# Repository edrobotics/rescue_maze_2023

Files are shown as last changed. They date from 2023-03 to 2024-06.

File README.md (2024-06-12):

# Rescue Maze 2023

Repository for ED Robotics' participation in Robocup Junior Rescue Maze 2023.

The code was used in the RoboCup SM (Swedish championships) and in the RoboCup worldchampionship in Bordeaux. 

## Scores: 

- RoboCup Junior Sweden 2023: first place

- RoboCup Junior 2023: top 10 (or tenth place if you prefer it that way) 

- RoboCup Junior 2023 superteam: third place together with Bot Ugl-EE from Australia

## Notes:

It was our first year doing Robotics, so please enjoy the spaghetti<!---and don't forget the sauce-->.

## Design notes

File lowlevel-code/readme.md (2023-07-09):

# Auriga (lowlevel) code
This code is for the code running on the auriga, which includes sensor interaction, motion system, and rescue kit mechanism.
The competition is now over, so hopefully nothing in here will have to be touched ever again.

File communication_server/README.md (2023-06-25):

# README
This application is the server handling communication between the programs on the raspberry pi as well as the communication between the raspberry pi and the auriga.

In its current state, it is just some code put together as a base and it does not work yet.

In "communication_protocol.md", the communication standards are written down.

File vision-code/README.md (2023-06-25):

#Vision code folder
This code will run on the Raspberry Pi

to start
python3 control_class.py

to move programs to pi if git is not working
./rsyncmaze.sh
#you have to edit local path

to move log from pi 
./updatelog.sh
#edit local path aswell

to move last run to a folder
python3 archiv_log.py

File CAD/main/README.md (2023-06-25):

# Main CAD files
This is the folder for all CAD files except for the rescue kit mechanism.

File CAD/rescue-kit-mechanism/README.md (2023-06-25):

#Resue Kit Mechanism CAD files
This is the folder for the CAD files for the rescue kit mechanism.

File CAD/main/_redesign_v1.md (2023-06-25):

# Redesign v1
This is the first redesign after the swedish competition

# Problems with old design
- Robot jumping/skipping when turning
- Turning was not really around center point.
- High CG - the robot is constantly close to tipping over when driving on ramps
- Difficult to work on the robot
    - Wires inaccessible -> cannot secure them, among other things
    - Time-consuming to disassemble
    - Annoying to change battery
- Lack of space for rescue kit mechanism
- Rescue kit mechanism prone to breaking
- Battery cable touching wheel while driving
- Electrical connections not always shielded
- Not enough space for raspberry pi camera ribbon cable

Unsure/speculation/potential problems
- Front sensor may be positioned too low and may be too narrow and too unstable
- Too small FOV for the camera

# General improvements
Certain:
- Lower CG
    - Power the raspberry off of the main battery
    - Put the pi lower down
    - Try to sink everything down a bit into the baseplate.
    - Place dummy weights down low?
    - Longer wheelbase - would make turning worse
    - Alternative solution to lower CG: Add some kind of support wheels which engage only when the robot is tipping too much. A challenge to keep them away from the walls during normal operation.
        - Wild idea: Use servos or similar to control the arms
    - Alternative solution to lower CG: Drive slower up the ramp (if even possible?)
    - Move voltage converters lower down.
- Make the robot easier to work on
    - Improve ease of (dis)assembly - not everything should be connected by the same screws. Not too many components per screw.
    - Make the top come off -> can access everything easier
        - Slice the pillars somewhere above the ultrasonics
        - Mount the mirror to the top, with arms comming down
- Mount the encoder motor drivers better. Remove pins and make housing.
- Add possibility to stabilize the rescue kit tower by connecting it to the pillars
- Add lighting to the camera

Maybe:

# New notes

Hold the mirror with two arms going down on each side, fastening where the support legs meet the rest of the body.

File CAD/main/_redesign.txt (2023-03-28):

Things to change/update/add in the redesign:

/Move the back motors inwards and increase the spacing to an appropriate amount
/Move the ultrasonic sensors inwards a bit
	/The front bracket can be partly under the auriga
/Maybe put ultrasonic sensors sideways to improve camera view?

/Make the baseplate thicker
	/-> Enables the battery to be sunken in if needed
	-> Allows space for the rescue kit mechanism

/Battery mounting:
	/Remove the baseplate and make the battery mount separate
	
Colour sensor mounting:
	Flap that can move up and down
	
/Rescue-kit mechanism mounting:
	XSome removable plate in the back
	/Mounting holes for plate added.
	
Mirrors go on top of the auriga. The same assembly could hold the mirrors

/The carrying handle can Go on the back, alternatively from front and back up to middle

Fixes:
/The slot for the ledring could be a bit larger and the supports in front could clamp down from above
/The holes for the pi should be deeper

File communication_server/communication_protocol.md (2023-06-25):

# Communication protocol - sockets
Communication is always initialized by the client sending a request.
After the client has sent a request, serialServer will either fetch the requested data or execute the given command.

In general, every request should be answered with the requested data (if there is any) and then some message signalling that the command was executed.

Maybe every request should be terminated by some special character (like \n)?

## Requests

### Drive step
Drives one step in the maze.
- Arduino function - driveStep()
- Arguments - none
- Return - whether or not a full step was driven. Returned as '1' or '0' (as strings/chars), as well as the ground colour of the tile that would have been driven on. Also the reason for not driving a full step?
  - Reasons can be odometry error, ground colour, error detecting the wall with the ultrasonic etc.
  - TODO: What should the maze program do if there has been an error in the odometry? Does it need any other data from the auriga?
- Request - "!driveStep"

### Turn steps
Turns the specified amount of steps (not yet implemented) in the specified direction.
- Arduino function - turnSteps()
- Arguments - the direction to turn (cw or ccw)
- Return - none
- Request - "!turnSteps, *direction*"
    - *direction* - cw (clockwise) or ccw (counterclockwise)

### Get wall states
Returns the current state of the walls around the robot
- Arduino function - getWallStates()
- Arguments - none
- Return - String containing comma-separated 0 and 1 representing if the walls are present (1 is present) in the format: "*front*, *left*, *right*", where front, left and right are the values for the corresponding walls
- Request - "!getWallStates"

### Rescue kits (to be done)

### Get victim state
Returns whether or not a victim has been detected (and how long ago the response was?)
- Arguments - none (maybe maximum time since last discovery?)
- Return - The victim type and whether it is on the right or left side of the robot.
  - "*victimType*, *victimSide*"
- Request - "!getVictimState"

Note: The code will probably check if it has a victimState stored and how long ago it was stored. Then there will be another process/thread (?) which responds to the vision program and updates these variables which can then be used in other ways.

One problem with storing the victimstate is that if the robot turns, the directions will no longer be correct. Maybe this program should also keep track of absolute direction (given by the maze-code in every command altering direction?). Maybe it will not be a problem if we never use victim data that is too old.

General about vision - The program on the auriga will need to be able to stop in the middle of a driveStep to detect a victim, and the maze-code (and this server) will need to be able to accomodate that as well.

### Update victim state
Gives data to serialServer about victim type and position. Sent from the vision-code.
- Arguments - "*victimType*, *victimSide*"
- Return - None
- Request - "!updateVictimState, *victimType*, *victimSide*"

# Communication protocol - serial
This section handles the communication between serialServer and the auriga.

## General communication format
Data will either be sent as chars and the termination character will be '\n'.

Commands: !\<command>,\<data>'\n'

Return: !a,\<data>

Return !s (success) or !f (failed) when done with an action

!b may be used for sending debugging information from the auriga to the raspberry (?).

## Commands
- !d - driveStep
  - Return:
- !t,\<direction> - turn
  - direction - which way to turn. 'r' (right), 'l' (left)
- !k,\<amount> - drop rescue kit
  - amount - the amount of rescue kits to deploy (maybe not used?)
- !w - getWallStates
  - !a,\<walldata> - walldata is a byte where the 3 last bits represent the wall states. 0b\<front>\<left>\<right>. 1 is present, 0 is not present.
- !i - interrupt the current action
- !r - resume the current action after an interrupt

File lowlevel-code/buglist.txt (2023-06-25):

When driving away from a wall, sometimes the back wall change is not detected and the front one is used instead

When doing gyroturnsteps, it sometimes turns the wrong amount. WHY?

The first gyroturn without a preceeding drivestep could have some zero-variables

When driving onto a colour, the robot stops too late

Communication features to implement:
Tell colours (sort of done)
Tell if ramp driven up

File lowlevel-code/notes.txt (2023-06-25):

Make a function to calculate the difference between any angles - can replace some code present now.

gyroTurn() - can turn more than 180 degrees. Divide it into < 180 degree segments.

General - add some way of filtering out unreasonable results and falling back to "dumb" methods in those cases.

General - if I call the MeUltrasonicSensor::distanceCm() too rapidly, will the distances update every time?

The method to check for wall changes will have to be updated - right now it will fail if a sensor mistakenly measures so wrong that the wallPresence changes.
    Maybe calculate some kind of average and round it to 1 or 0? (so that a temporary error won't destroy everything)

Design of driveStep(): Should the checks modify trueDistanceDriven or should they just break and then the program will decide outside of the loop whether the distance has been drive or not?

Note: I modified the source code of MeUltrasonicSensor.cpp to be able to specify the maximum distance measurement

Note: The last thing that worked alright (?) was not checking the back sensors for wallchanges. The problem with interference did appear (even though it should have).

Check colour sensor (and others) in getUltrasonics.

Instead of moving every measurement in the array, keep the current index and just change that value. Could also calculate the average more efficiently.

Calculation of the current angle for use in the next angle should be separated out into its own function.

How and when is g_gyroOffset updated?

Add a requirement that trueDistanceDriven is close enough to what it will be corrected to when a wallchange is detected

When driving backwards, the detected wallchanges will be wrong. To do correctly, make an expression taking the target distance into account (or the starting distance, or maybe just special case for driving backwards)

Bugs:

Sometimes when the robot is close to a wall, it drives slowly forward and sometimes does not recognise the wall. (potentially fixed?)

Sometimes when the robot is driving without walls and you correct it (maybe something else is triggering it), it drives in a circle and does not drive backwards when it is stopped.
The trueDistanceDriven seems to be wrong (oscillates because the robot is driving in a circle)
Why is the robot not correcting accordingly with the data? The angles must be wrong (is this the same issue as the bug below?)

When the robot is going backwards, something seems to go wrong with the angles (it makes a "three point turn" but with an arbitrary amount of points and the oscillation gets larger every time)

Sometimes the robot does not correct the right amount when turning.

Sometimes (often?) when a backwallchange should be detected it is not and the frontwallchange is used instead.

The robot does not seem to stop directly when detecting a new ground colour - instead it looks like it always drives the 30cm it should. Why is that?
Should have been fixed. Was probably caused by an inverted return statement (but I have NOT tested if it works now!)

Other (not necessarily bugs, but things to fix):
In driveStep(), when the first measurements are taken, the robot only uses one wall even if both are present.

After you have stopped, flush the distance arrays and update the robotAngle somehow. This should also be done before and after turning.

The driveStepDriveLoop takes too much time. How can I improve it?
    Make the getUltrasonics() function take less time
    Perhaps not calculate the angle every time (how much time does it take?)- just the difference? Then calculate the angle only when needed (say when you left the wall you calculate the angle based on the previous data. also in the end)

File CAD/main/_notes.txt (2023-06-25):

TODO:
Check ultrasonic sensor heights
Addd a front ramp to aid in driving over speedbumps
Idea - add small wheell beside the coloursensor -> it can sit down low and still be safe from impact, because the wheels will lift it if it drives over something

General:

Holesize is maybe a bit to small
	On the creator 3 it is OK, a bit tight, on the Prusa Mini it is too tight (you can still screw it through though)

Ultrasonic sensors:

The ultrasonic sensors should be higher up or could be angled slightly upwards to avoid falsely detecting a ramp as a wall.

Baseplate:

Ska båda motorkonfigurationer fungera med samma basplatta?

Om plasten ej fungerar kan CNC-maskinen vara ett alternativ

Ska måttet som anges vara för hjulbasens mått eller för basplattans?

For threaded inserts: https://hackaday.com/2019/02/28/threading-3d-printed-parts-how-to-use-heat-set-inserts/

Gör mount-stället för ultrasonic sensor brackets smalare (på hödjden)?

Improvements for next print:
	Add holes for rescue kit mechanism

Batteri + hållare:

För att byta batteriet: Borde kunna dra mellan hjulen

För att hålla fast batteriet: Kanter i sidan. Någon form av rem ovanför för tryck nedåt. Alternativt tryckplatta?

Rescue kit mechanism:

Perhaps use rack and pinion for the pusher for the rescue kit mechanism?

Use some heavier weight and put on top to make the rescue kits go down more reliably?

Design ideas:
	Have a rescue kit holder (like a well) with an extended "backwards" edge. A rescue kit is in the well, it moves, the rescue kit drops out as another one drops onto the "backwards" edge. When the mechanism retracts, the rescue kit on the "backwards" edge is pushed into the well by the back wall. This works both with linear and rotational motion.

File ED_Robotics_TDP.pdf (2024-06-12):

## ROBOCUPJUNIOR RESCUE (MAZE) 2023

## TEAM DESCRIPTION PAPER

## ED Robotics

### Abstract

This paper describes our robot, as well as the development process of it. The robot is a junior rescue maze robot capable of completing most tasks that are within the rules. It is a fourwheeled encoder-motor driven robot controlled by a Raspberry Pi and a Makeblock Me Auriga (Arduino Mega). Positioning is done using two ultrasonic sensors on each side and one in front, and the rescue kit mechanism is in the back. For detecting victims, the robot uses a camera looking down on two mirrors, which split the image into two, enabling us to see both walls simultaneously. The strong sides of the robot, besides being cute, are advanced pose estimation, aligning itself well to the maze, optimization of memory usage and a reliable rescue kit mechanism.

### 1. Introduction

### a. Team

The name of our team is ED Robotics, and our members and their roles are as follows:

QUAK123 – Responsible for rescue kit mechanism. Prior experiences include programming games, mobile and web applications. Worked on CAD projects in school.

apollen85 – Responsible for the motion system. This includes the hardware design (excluding the rescue kit mechanism), electronics and local maze navigation (for example turning exactly 90O). Experience was gained through experimenting with simple Arduino projects and doing CAD projects at home and in school, but organized and complicated projects like this one have not been attempted before. Programming was selftaught.

c4tm4n/"bohrmeister” – Responsible for the vision system and the raspberry Pi. This includes detecting coloured and visual victims and handling the raspberry Pi. Past experiences include python programming and Linux skills.

MrK – Responsible for maze navigation and mapping. This is also the master code which communicates with the other programs, and it also navigates the robot through the maze, maps the maze, and gets the robot back to the start tile. Had previous experience in programming, both from selflearning, for instance from making games, and from school.

### 2. Project Planning a. Overall Project Plan

As this is our first extensive and collaborative project, our overall aim for the competition is learning about collaboration and robotics as well as building a well-performing robot.

During the early stages of development, not much of a plan existed. However, we realised that we needed to spend much time as early as possible. Later on, our work became more organized. A schedule was made and evaluations were made throughout. Different roles were assigned and defined, which enabled us to work more efficiently. The plan was to be mostly done with the robot a few weeks before the competition to give time for extensive testing and bugfixing.

Some of our milestones have been to get the components to work independently, so that the robot could be tested in its complete form. Other than that, not many milestones were set.

As we have no past performances, these have not influenced our development process. Inspiration has been taken from other teams in designing our solutions, but a lot has been done without any prior research or experience.

### b. Integration Plan

The system is divided into many parts. Processing is done by a Raspberry Pi, running navigation code and vision code, and an Arduino, running lowlevel code. These communicate via serial communication and communication between programs on the same Pi is done via socket communication. The lowlevel code handles all hardware interaction, which mainly consists of driving the four encoder motors, reading ultrasonic distance data, reading gyro data and controlling lights. The rescue kit mechanism is on its own removable plate giving modularity, and the only electric connection is the servo wires.

### 3. Hardware

The robot is a four-wheeled robot built on a baseplate, on which everything rests. The two arcs support sensors, computers and more and the battery has been mounted on the underside to lower the centre of gravity. A large open space in the middle of the robot on the top enables us to have a dual-mirror system, through which the camera on top can see the wall on both sides of the robot simultaneously. This has forced us to squish everything out of the field of view of the camera, which has proven to be difficult at times. To make assembly easier, we use M4 screws and nuts for everything big enough and M2 for everything smaller. Electrical
connections have been made using either direct soldering,
dupont-connectors or other connectors specific to the

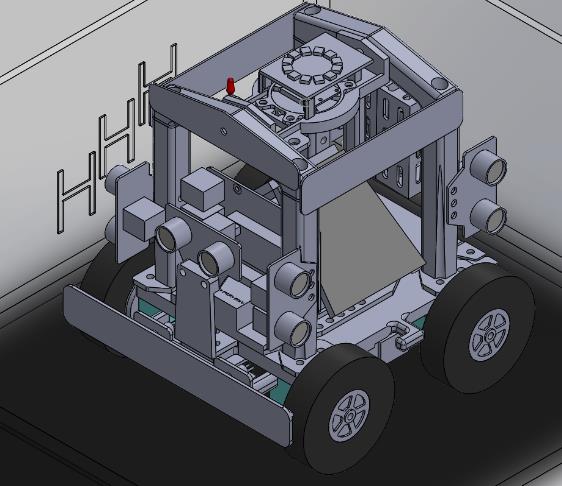
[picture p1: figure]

sensors/components used. The dupont-connectors have been secured, for example by using hot glue, to prevent accidental disconnections.

### a. Mechanical Design and Manufacturing

The main structure of the robot consists of 3D-printed parts. Everything is connected by the baseplate. From the baseplate, 2 arcs come out supporting the sideways-facing ultrasonic sensors and leaving the middle open for the dual-mirror system. The top of each arc is removable to facilitate access to components under the mirrors, which are held in place partly by interfacing with the board below.

The power train consists of four encoder motors from makeblock. The wheels are neoprene foam tires with a 3D-printed mounting adaptor attaching it to the motor, but textured silicone tires are available as a backup. The size of the tires was decided by adjusting the size in our CAD model and then, using the appropriate constraints/mates, the ground clearance was checked when driving onto and leaving ramps from above and below. For ground clearance regarding speedbumps, simple calculations were made to calculate the distance from the ground to the lowest point of the robot. Placement of the motors and thereby wheels was made to minimize skidding while turning (put close together along the length of the robot to minimize lateral movement), while also leaving enough space below for the battery and not making the robot too wide. For the outer part of the backup wheels (the tire), some different materials were tested. Slick rings worked alright when clean, but they got dirty quickly and lost grip. Some thicker and wider tires with a more pronounced structure (our backup) were also tested and yielded

Fig. 3.1 – CAD model of the robot and surrounding maze better results. Mitigations for the wheels sliding along speedbumps at shallow angles include perforated edges, software fixes and potentially protrusions on the sides of the wheels.

The main concept of the rescue kit mechanism is to drop rescue-kits by pushing them over the edge of the robot, using a racket and pinion mechanism. The rescue kits are stacked on top of each other and stored in a container. The container is designed in a robust manner to withstand bumps in the case of the robot overturning and a support for the container can be applied to make it less fragile while being transported. The entire rescue kit mechanism is built on its own plate that then is mounted on the main baseplate of the robot. This is done intentionally to avoid having to print the whole baseplate of the robot when making small changes that only affect the rescue kit mechanism, thus saving time and materials.

One aspect of our robot which we believe to be fairly unusual is the dual-mirror system. It is our chosen solution to the problem that the Raspberry Pi only has one camera port, while we want to see both walls simultaneously. Because we had the hardware for the mirror system and did not know about the existence of dual-camera solutions, we went with the mirror system. Other considerations like the extra processing power needed to process two images were also taken into account. The size, positioning, shape and angle of the mirrors were determined by trial and error. In the
CAD model, lines were drawn from the camera lens
centre to the vertices (corners) of the mirror, to the wall
of the maze the robot was positioned in.
In order to satisfy the law of reflection, constraints were added to set the angle between the outgoing line from the camera and the line normal to the mirror and the angle between the outgoing line from the mirror and the line normal to the mirror to equal values. This resulted in 4 intersection points between the outgoing lines and the maze wall. When connected by lines, the

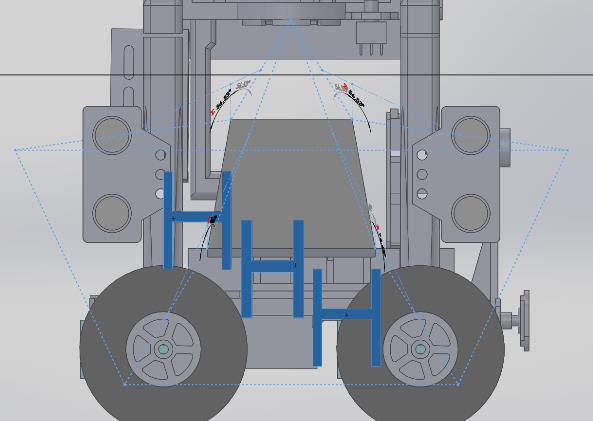
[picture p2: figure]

area created forms the FOV (Field Of View) of the camera.
As mentioned earlier, the characteristics of the mirrors
were changed to get an optimal view of the wall and the victims painted thereon. To make this process easier, victims were drawn on the maze wall in the CAD software at the ideal height as well as on the maximum and minimum height, ensuring that all legitimate victim positions were covered.

### b. Electronic Design and Manufacturing

The computing power of the robot is provided by a Raspberry Pi 4 and a Makeblock Me Auriga, which is a modified Arduino Mega. The Pi is the main brain of the robot, responsible for maze navigation and vision processing due to its greater processing capabilities, while the Auriga handles sensor interfacing and maze navigation from tile to tile due to it being easier to integrate with the hardware and it giving the precise timings needed for measuring distances with ultrasonic sensors or reading encoders accurately, for example. Both of these boards are powered by a single 1800mAh 3-cell (3S) LiPo battery through two voltage regulators (XL4015) connected to the battery in parallel. The Pi receives its power through a cut USB-C cord with a voltage of 5,1V (as per the specification of the Pi) and the Auriga is connected by a barrel connector supplying 9V (specification says 6-12V). The reason for powering the Auriga with 9V instead of 5V like the raspberry is that the motors need the higher voltage for operation and the board cannot step the voltage up, only down. Both of these voltages are regulated down from the 10-12,6V which the battery can supply (10V is our safety minimum at roughly

Fig. 3.a.1 – Camera FOV

3,33V/cell). The battery was placed under the baseplate to keep the centre of gravity low, aiding in the stability of the robot. Communication between the boards is done by serial communication but is complicated by that the Auriga runs on 5V logic and the Pi on 3,3V logic. This is solved by having a logic level shifter between the connections, which can convert logic signals between two given voltages (5 and 3.3V in this case).

The robot has several sensors. For driving in alignment with the maze, it has encoders on the motors, ultrasonic distance measurement sensors and a gyroscope. Each wheel has an encoder built in and there is one gyroscope built into the computer responsible for the low-level tasks. The encoders are the default distance measurement sensors for knowing if the robot has driven a “step” (30cm, one tile) but due to their unreliability regarding tire slippage and possible debris, other methods later described are used in conjunction with the encoders. The ultrasonic sensors are used to align the robot to the walls of the maze. There are two on each side, meaning that even with just one wall being present we can calculate the sideways position and angle relative to the wall (fig. 4.a.1). However, the ultrasonic sensors were observed to be noisy (values jumping up and down), so to smooth the values out, a running average for the measurement of each sensor is kept. A sensor in front is also used to determine the distance to the wall in front and stop when close enough, and it may be used for determining distance driven instead of using encoders. Because of the relatively slow time of flight for the sound waves produced by the ultrasonic sensor, interference and dead time on the processor were real problems. Therefore, the sensors are queried in a certain order with active delays in between. The gyroscope becomes useful when turning and when driving without a wall. It can keep track of the rotation of the robot very precisely for the short amount of time it is used, as drift does not have time to pick up and a new reference is established every time before the program relies on the gyroscope.

Another sensor is the colour sensor near the ground on the front of the robot. It sits as close to the ground as possible while still being safe and guarded from speedbumps, debris and steps, and it is used to determine the colour of the ground under or slightly in front of the robot. It is an Adafruit TCS34725 and the integration time is set to 60ms to get updates frequently enough so that the robot does not accidentally drive too far into a black tile before driving back. The camera could also be considered a sensor, but the details of that assembly has already been given in 3.a.

For powering and controlling the encoder motors, two new encoder motor drivers were needed. Because there are only two built-in encoder motor controllers on the Auriga and we needed four of them, as driving one side per controller did not work good enough, we found a way to use two more. There is another board from Makeblock called the MegaPi, for which encoder motor controllers with the appropriate port and the same library are available. Through reverse-engineering the drivers on the board using schematics for the Auriga as well as the MegaPi, combined with manual measurement, we were able to connect the two new drivers to the Auriga, define two new encoder motor ports in the library and then use these identically to the original ones.

### 4. Software a. General software architecture

The software is divided into three different programs. On the Auriga, we have the low-level code, which is responsible for hardware interaction (except for the camera) and navigating from one tile to the next, through ramps and turning. The two other programs, which run on the Raspberry Pi, are the vision program, which detects victims and sends that data, and the navigational program, which makes decisions about navigating through the maze, stores information about the maze, and decides when rescue kits should be dropped.
The navigational program can send commands to the low-level program, which is constantly listening. During execution of certain commands, the low-level program can accept interrupts for stopping and dropping rescue kits, after which to finish the command. When a command is finished, the low-level program sends a command to the navigational program so that it can continue the process. This interface is held constant and the implementation of commands does not matter to the other party. For extra redundancy, some features have been implemented, like always answering commands for confirmation.
The navigational program also receives information about detected victims from the vision program, like how many kits we should drop, and on which side the victim is on. The data is checked, to make sure that there is a wall to that side, and then forwarded to the low-level program, which blinks and drops the kits. To make sure that the navigational program always listens to the vision program, a separate thread is used for listening. Orientation in the maze is done by the low-level code using primarily the ultrasonic distance sensors. Because two sensors are used for each side, we can theoretically get an exact value for the distance and angle of the robot in relation to the wall:

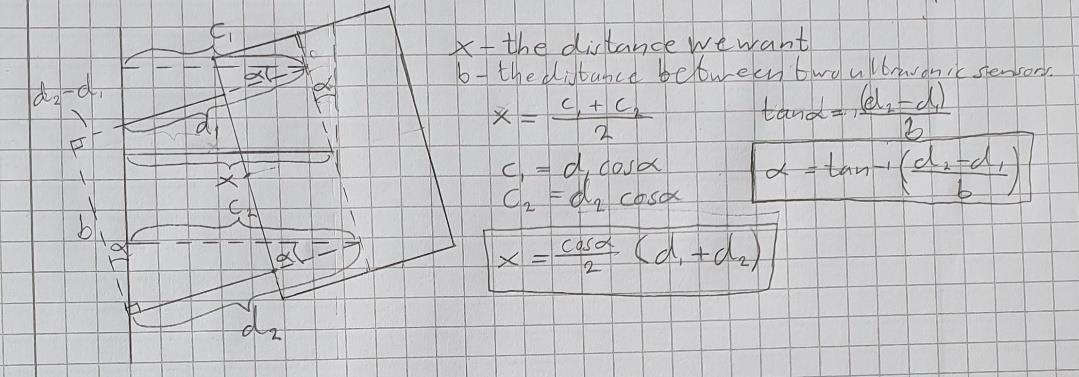
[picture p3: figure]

Fig. 4.a.1 – Calculation used for pose estimation
This is very good in theory, but due to some inaccuracies in the ultrasonic sensor readings there are slight fluctuations. Thankfully, this did not prove to be a problem, partly due to the smoothing of ultrasonic sensor measurements using a running average. To position ourselves in the middle of tiles in the sideward direction, the distance to the wall is used in a PD-loop (PID without integral term) to give a wanted angle, which is in turn fed into a PD-loop which gives the wanted motor speed corrections. The robot angle is also used to calculate the distance driven parallel to the wall. Using trigonometry we can calculate this distance with the robot angle and encoders’ measure of the distance driven.
Ground colours are detected by the low-level code using a colour sensor which gives values for red, green, blue and clear. Each colour that we should be able to detect has a reference colour with the four values and a radius. A colour can be seen as a point in a four-dimensional coordinate system, and thus, when a colour is read we can calculate the euclidean distance between the colours, the parameter distance. Distance is calculated to all reference colours and the radius is subtracted, after which the closest one is picked. The radius is a measure of how spread out the values are. This code is wrapped in a class for modularity. For detecting blue and reflective tiles, a high enough share of measurements on the new tile have to confirm the decision.
The read function in the library for the colour sensor is blocking, meaning that it blocks other code from executing during that time. This is problematic because we cannot have any “dead” time in our control loop. In the read function, there was just a simple delay equal to the integration time followed by reading the sensor over I2C, so to fix this, the delay was removed and instead it is checked every time the read function is called whether the integration time has passed since the last reading.
When dropping rescue kits, the low-level code blinks simultaneously to dropping the kits to save time. This is achieved by using similar methods to the colour sensor, with there being a while loop containing if-statements, which are only executed if enough time has passed since the last execution of that if-statement.
Driving a step is done as follows:

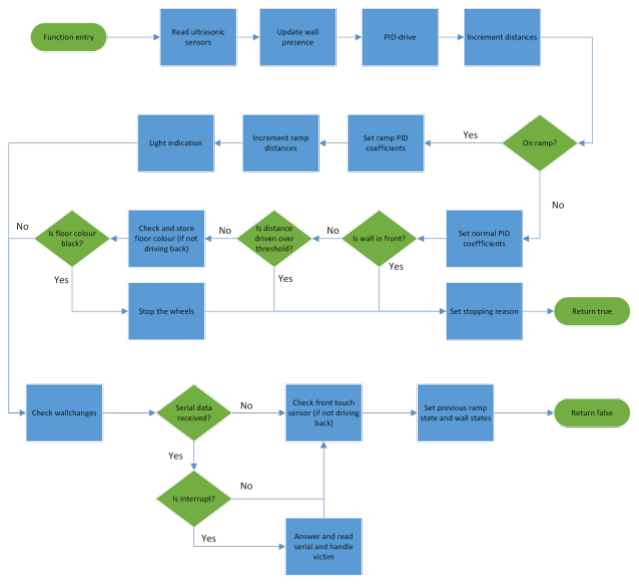
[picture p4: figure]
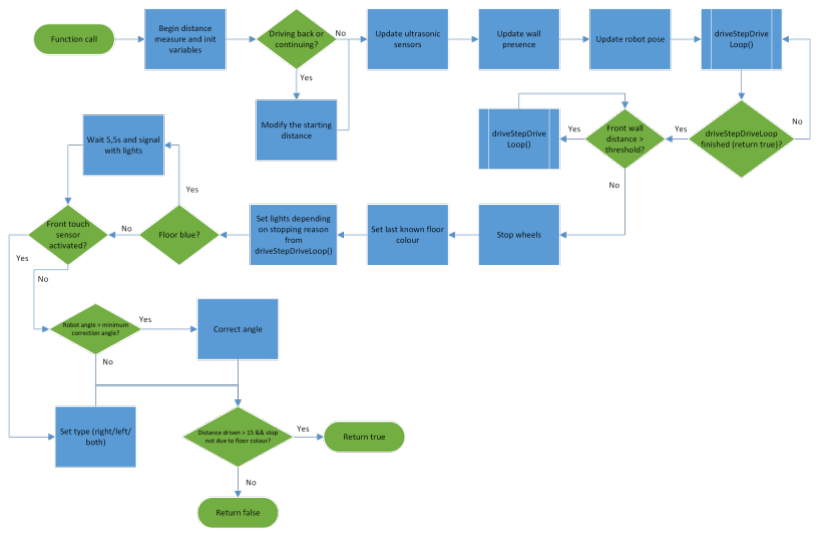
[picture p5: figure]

Fig. 4.a.2 – Flowchart for driving a step | Fig. 4.a.3 – Clarifying flowchart for the driveStepDriveLoop() subroutine

To store data about the maze, the navigational program uses a list of a class called Map, which contains a 50 by 50 unsigned 16-bit integer two-dimensional array/matrix, where each position in the array represents a tile. For each level we visit, we add an instance of it to the list, so that we can easily change our position in the maze and level by changing the index in the list and in the map array. We store our position with three integers, one which keeps track of which map we are on, one that contains our X-position, or “left and right”-position, and one which contains our Z-position, or “forward and backward”-position. To keep track of which direction we are facing, we use an integer which can have four possible values for front (=0), left (=1), back (=2) and right (=3), which have the same values as the bit indexes in the stored map, so that I can convert directions directly to walls. If we for instance turned left, the direction would be incremented by 1. Since we do not want the value of the integer to be larger than 3, or smaller than 1, we make sure that we add or subtract 4 to it, if it is larger or smaller than that, after each time we update the direction. Each bit in the 16-bit unsigned integer is used as a boolean, which is possible due to bitwise operations, as we can use AND when checking for a value and OR, or NOT AND when setting a value in the integer to true or false respectively. If we were to utilize all the 16 bits, it would be about 90% more memory efficient (as 1 bit is 1/8th of a byte) than using regular booleans.
When we travel up or down a ramp, the low-level program will send the height and length of the ramp, which is calculated using trigonometry. The navigational program uses this to calculate how high up we are compared to the first level, and how many tiles forward we moved. This way, we can figure out whether a ramp leads to a new or known map, and we can keep track of where we are on a level even if there are multiple ramps to that level, as well as reduce the amount of memory required.

To navigate the maze and to ensure that we can explore the entire maze if there is enough time, the navigational algorithm based on Trémaux's algorithm. The algorithm is typically used as a maze-solving algorithm, but if the maze has no solution, as the case is in this competition, it always explores the entire maze. As described in figure 4. a.4, our implementation of it starts by looking at the tiles around it for unexplored tiles. If there are any, they are saved in a list in the current map-object to keep track of which level the map belongs to. Then, the program turns and drives to one of the tiles. It first tries the tile on the left, then the tile in front, and lastly the tile to the right. After it has driven it checks the tiles around the new tile and the cycle continues. When it comes to a tile that does not have any unexplored tiles around it, it finds a path to the last saved tile using a shortest path algorithm and goes to that tile. When there are no unexplored tiles left in the map, it returns to the start tile, or ramps that are not fully explored, as I mark if we are not on the first level.

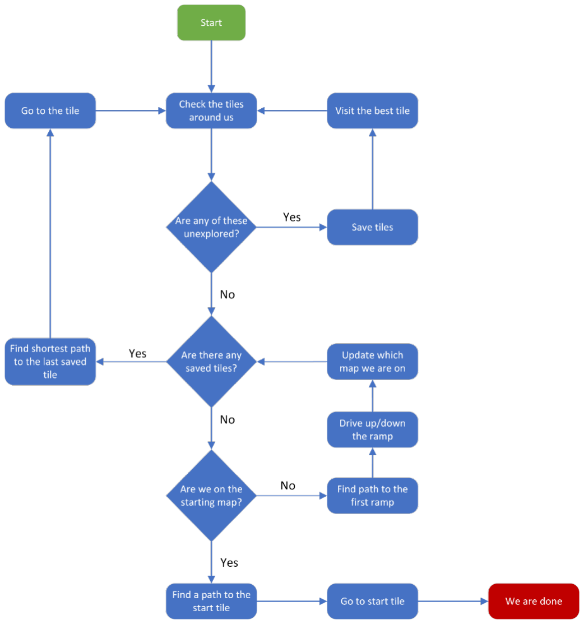
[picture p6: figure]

Fig. 4.a.4 - Flowchart for the navigational algorithm

To find a path back to the start when the time is almost up, or to any tile in the navigational algorithm, a recursive path-finding algorithm was developed from scratch. The algorithm works by checking the tiles around it, starting with the one closest to the goal tile. If there is no wall in the way, we check if the tile is explored, not black, not a ramp or if it is the tile we are trying to find, and if either of those are true, we move onto the next step. The tile can also not be in the current path. In this step, we add the tile to a list, which represents the current path, as a byte array which stores the tile’s X- and Z-coordinates. From here, we search the tiles next to this tile, and then the tiles next to those and so on, until we find the tile we are looking for. If we return without having found a path, we remove this tile from the path and mark it as a fully explored tile, which means that we will stop searching onto that tile. The shortest possible distance is between two tiles is adding the difference between the X- and Z-coordinates between the two tiles since we can only move in four directions. When we find our goal tile, we check if the distance to this tile is the shortest possible, and if so, we are done and return the found path. If this was not the shortest path, we begin returning to where we started, but we do not mark the tiles from the found path as fully searched, because there could be a shorter path that uses part of this path. When we are going back to the start and we are not on the starting level, or when we have explored an entire map, we also need to “jump between ramps” to find paths, by taking our previously used ramps to get back to the starting area. It would also be possible to use the travel time instead of tile amount for more optimization.

The vision code is creating an HSV and a binary image out of the captured image. The binary image is used to find visual victims, first it finds contours in the image which are compared with combined sample images. The combined sample images have been created by adding together samples for each victim using bitwise operators (AND & OR). Resulting in one sample with all pixels the victims needs and one with pixels it may have.

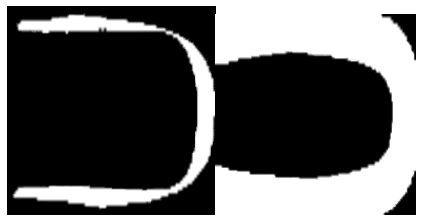
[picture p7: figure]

Fig. 4.a.5 – Combined sample victims for the visual victim ”U”.
The coloured victim identification uses HSV-thresholds to create masks. By analysing the mask, it makes sure it can be a victim by including factors such as size, position and difference to the surroundings. Furthermore, it also compares it with previous frames to make sure it keeps its shape.

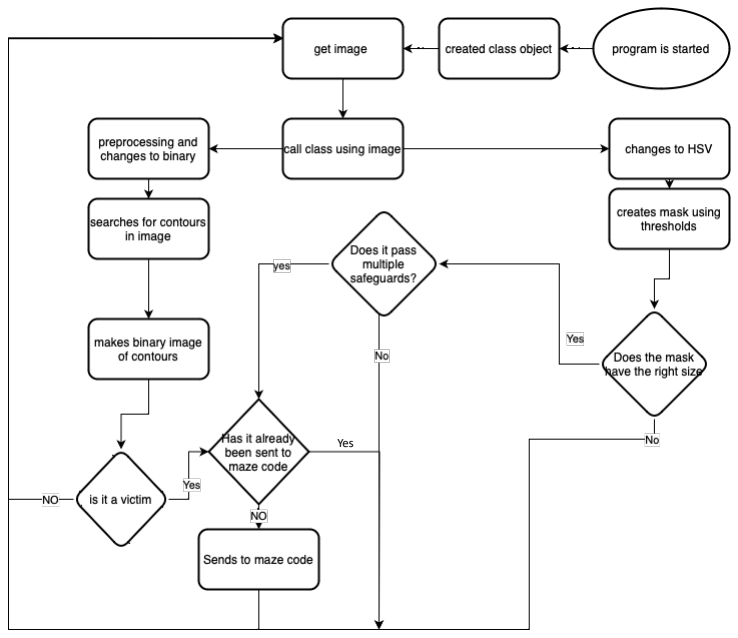
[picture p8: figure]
Yes

Fig. 4.a.6 – Flowchart for victim identification

### b. Innovative solutions

One important aspect of our odometry is something which we have named “wallchanges”. A wallchange is defined as when a wall is “lost” or “found”, that is, when the wall presence switches from true to false or vice versa. Because all walls begin or end at tile intersections, these detected changes in wall presence can be used to correct the odometry provided by the encoders and front ultrasonic sensor, which would otherwise be unreliable. Wallchanges give some stable point of reference. Wallchanges are calculated individually for every sidewards facing sensor which means that problems could arise if the robot angle is too great, as the wallchanges would be detected at the wrong distances. This is solved by using the current known robot angle and trigonometry to calculate the “true” position of the wallchange. When a wallchange is detected, we have a known reference to the robot position. That can be used to look at changes in the front ultrasonic sensor distance to determine how far the robot has driven.
Different testing procedures were implemented for the three distinct different parts of the code. In the lowlevel code, most new features were tested from the ground up, meaning that the function of the most fundamental functions was confirmed first, thereafter the functions “above” them and so on. This makes it easier to find errors as it narrows down the possible sources. Another type of testing is of the functionality of the robot that we actually want, and not the functionality that builds up to the goal. This testing was done by just letting the robot drive and when it encountered errors, it was stopped and the reason for the error was investigated. Elimination of behaviours correlated with errors was attempted with varying degrees of success. Not much raw data was collected due to the difficult nature of transferring it from the Auriga to the computer (an attempt was made with an ESP8266 but we never went through with it), but data was collected for setting thresholds (like distances to walls, measuring how far the robot drives, etc.).

There have been multiple approaches for testing the vision code. One has been testing it on runs with the robot, other options have been testing while standing and changing different factors. But the most common used is testing with previous captured log images. Sometimes the entire code was tested and sometimes only specific parts.

To test new features in the maze navigation code, there were two different possible procedures. Later, it was possible to test new features directly by running the code and trying to get the robot in situations that could test them and using a log file to find bugs and get data. Before the hardware was working, though, it was much harder to test the code. To counter this, a simulation of the competition was created, where code could be written and tested much quicker and easier. Without it we would likely not have time to fully develop the pathfinding algorithm or the navigational algorithm.

### 5. Performance evaluation

The performance of the robot is not as reliable as we had hoped for. We believe that the robot is a good prototype, but that it is not as polished as it should be. One of the big problems is that the robot is very reliant on the lowlevel code being able to drive perfectly, which is not the case. This makes the robot too complex for its own good, as a minor error in the lowlevel code could have negative consequences later. Mitigations for this have been tried, and work to an extent, but it could be better. Potential fixes would be to either make the maze navigation less susceptible to errors low down or drastic improvements to the lowlevel code, like better sensors and movement system (handling of stairs and speedbumps).

Testing has been done partly by testing the individual systems like described in 4b, but also by testing the robot as a whole similarly to how it would be during a scoring run. These tests were then analysed, and common failure points mitigated.

### 6. Conclusion

To conclude, this project has taught us a lot. Our goals were to learn about robotics, collaboration and having a wellperforming robot in the end, and we are of the opinion that these goals have been reached. A lot of improvements were found on the way, but due to a lack of time, they could not be implemented, and thus there is a lot of room for improvement. The robot has many good features, as outlined in this document, but there is much that can be done in terms of robustness and new features.

## References

- http://docs.makeblock.com/diyplatform/en/electronicmodules/maincontrolboards/me-auriga.html
- https://www.arduino.cc/reference/en/
- https://docs.arduino.cc/tutorials/generic/basic-servo-control

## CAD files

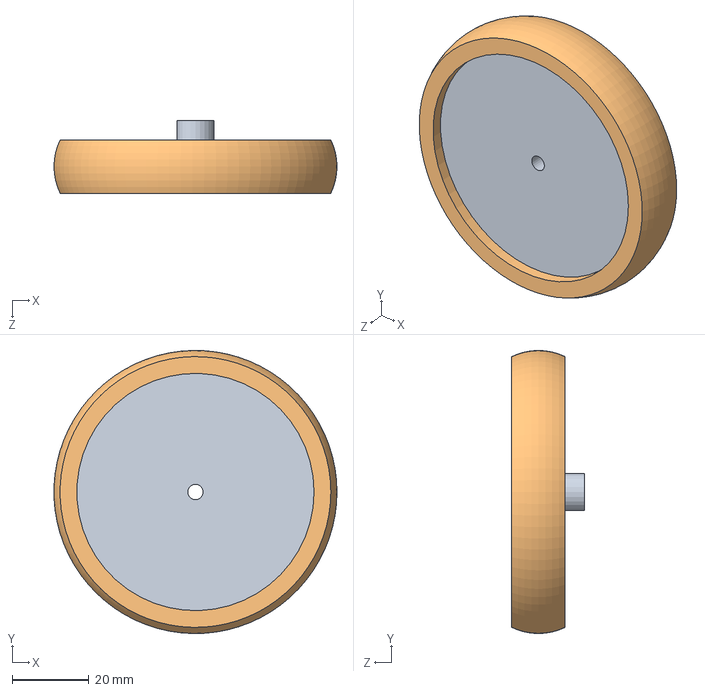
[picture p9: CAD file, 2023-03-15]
CAD/new-main/wheel_subasm.SLDASM
74.0 x 74.0 x 19.0 mm
wheels
tire

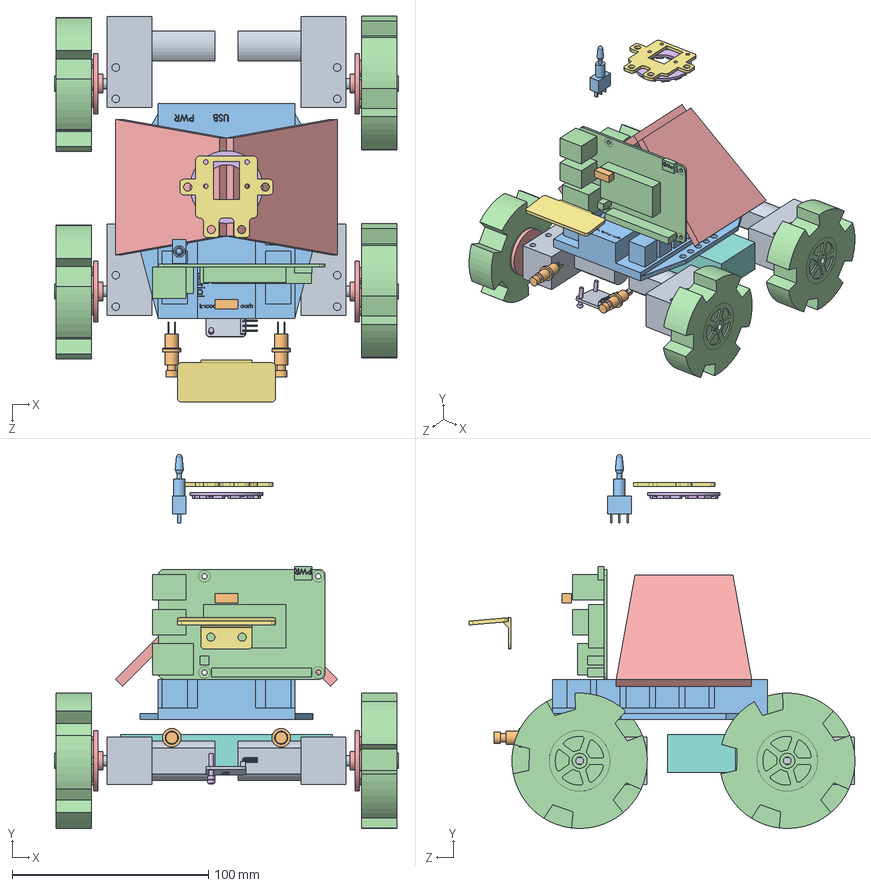
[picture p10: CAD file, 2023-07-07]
CAD/main/robot_asm_baseplate.SLDASM
175.5 x 190.5 x 196.6 mm
encoder_motor x 4
auriga_board
raspberrypi_4
mirror x 2
camera_LEDring
battery
coloursensor
front_sensor_button x 2
switch
neoprene_wheel x 4
neoprene_wheel_mounting x 4
M2.5_screw x 2
front_ultrasonic_sensor_shade

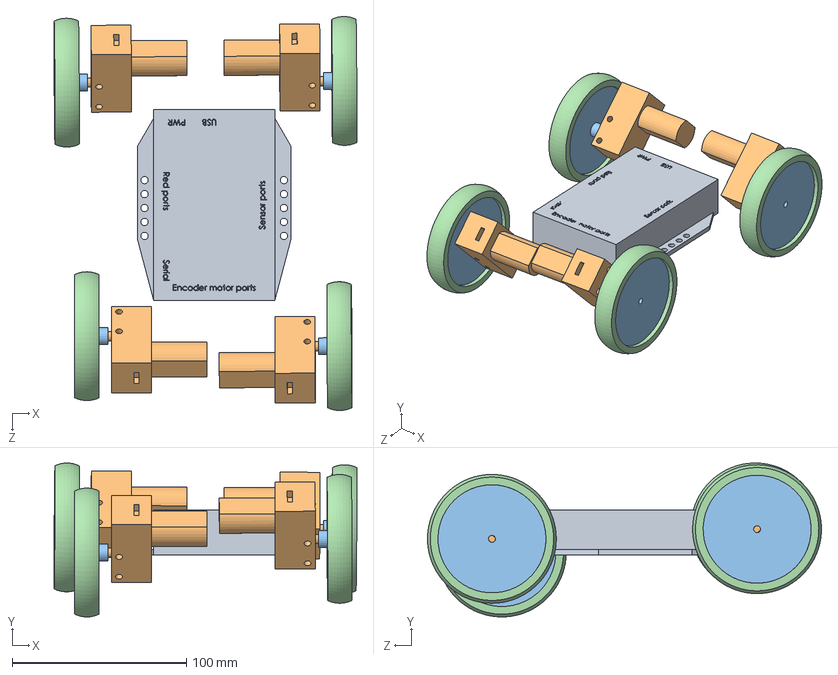
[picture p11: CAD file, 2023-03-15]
CAD/new-main/robot_asm.SLDASM
173.9 x 88.4 x 226.2 mm
auriga_board
encoder_motor x 4
wheels x 4
tire x 4

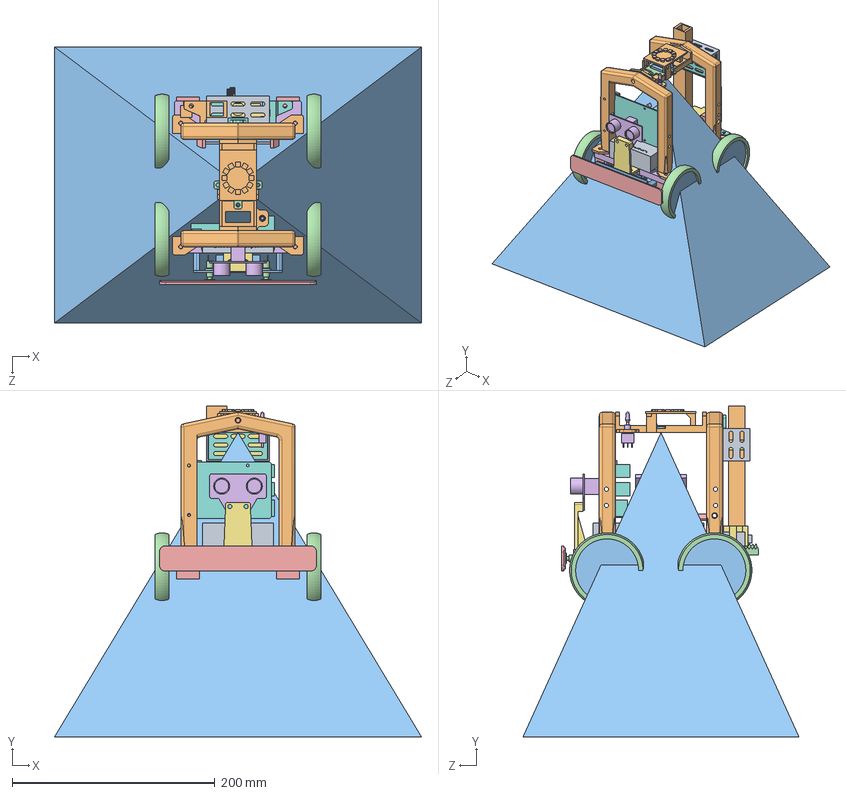
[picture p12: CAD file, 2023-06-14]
CAD/main/rescue_kit_mechanism/rescue_kit_mechanism_12_06_23/robot_asm_active_27.05.2023.SLDASM
361.9 x 326.2 x 272.2 mm
front_handle_ultrasonic-mount
wheels x 4
tire x 4
encoder_motor x 4
raspberrypi_4
auriga_board
battery
batteryholder
servo_placeholder
front_touch_sensor_bracket
front_sensor_button x 2
front_sensor_plate
switch
Behållare_31-05-23
baseplate_front_insert
spur gear_iso_12-06-23
baseplate
ServoHållare_03-06-23
rescue_kit_mechanism_plate
rack spur rectangular_iso

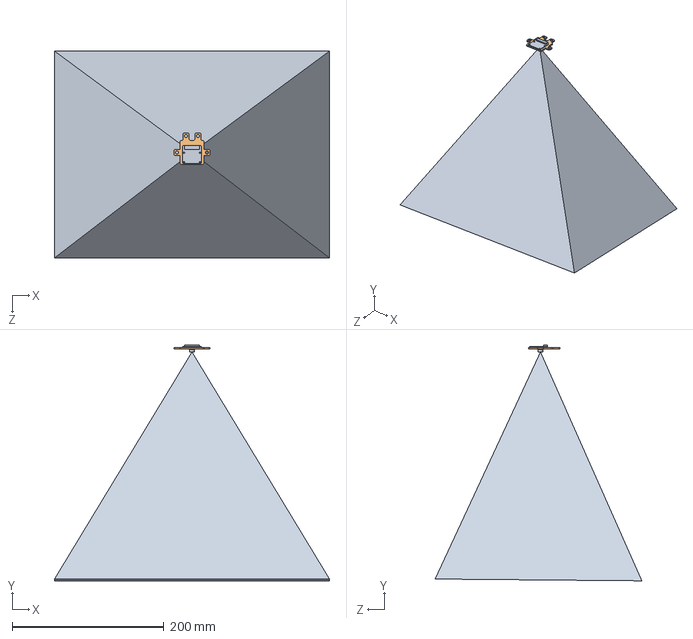
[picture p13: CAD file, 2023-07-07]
CAD/main/camera_holder.SLDASM
361.9 x 310.1 x 272.2 mm
picamera
camera_sled

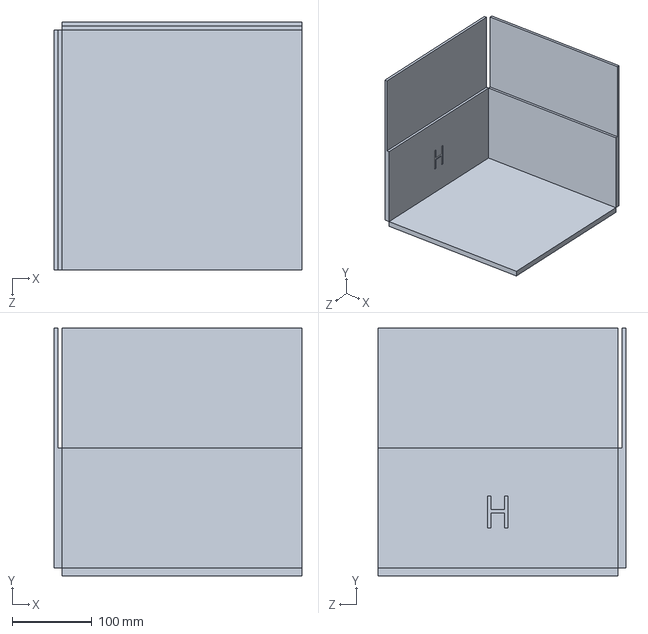
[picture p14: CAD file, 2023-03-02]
CAD/new-main/maze.SLDASM
310.0 x 310.0 x 310.0 mm

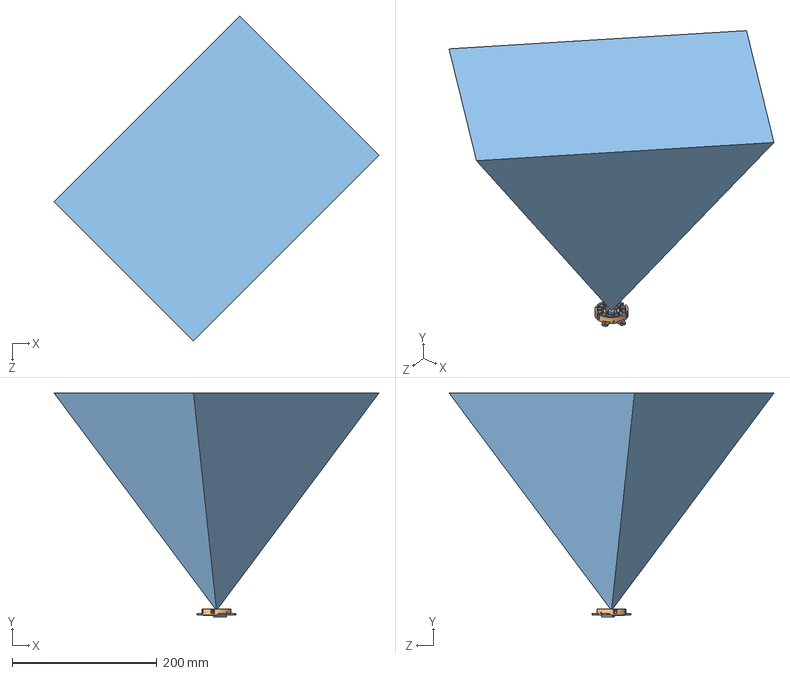
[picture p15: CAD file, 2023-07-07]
CAD/main/camera_LEDring_with_casing.SLDASM
448.4 x 309.0 x 448.4 mm
camera_LEDring
camera_LEDring_casing
picamera

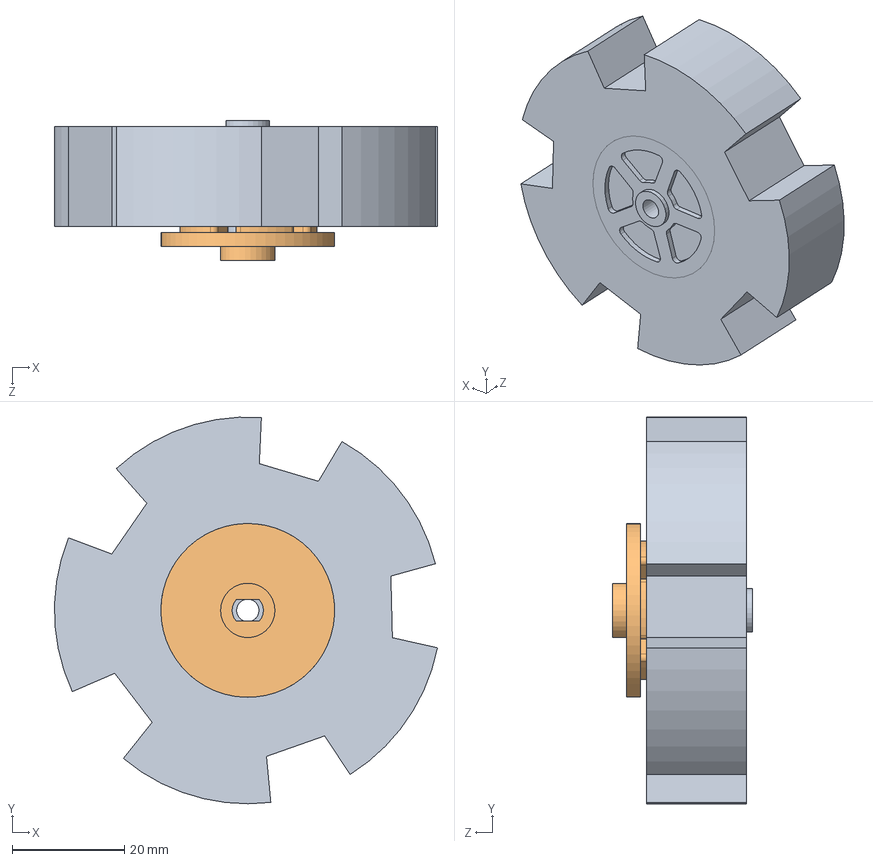
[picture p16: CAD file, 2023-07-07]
CAD/main/neoprene_mount_asm.SLDASM
68.3 x 69.0 x 24.9 mm
neoprene_wheel
neoprene_wheel_mounting

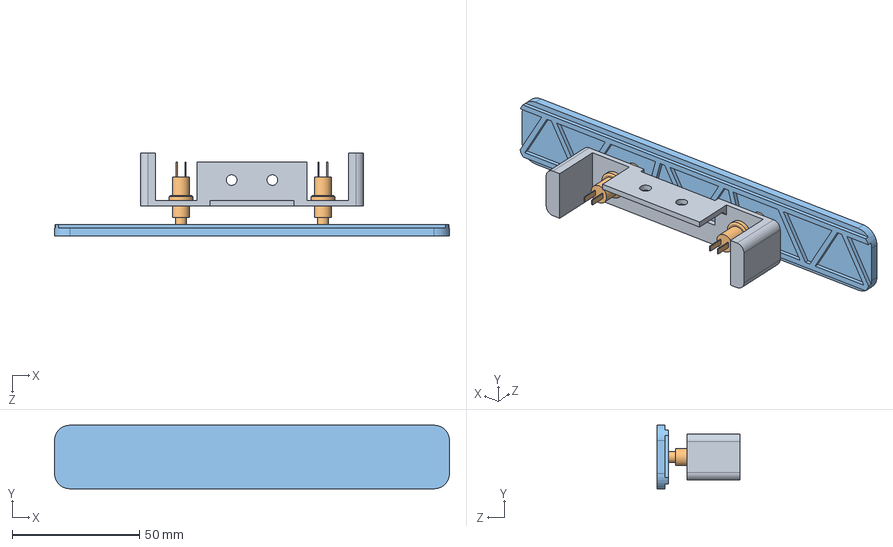
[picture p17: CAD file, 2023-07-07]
CAD/main/front_touch_sensor.SLDASM
155.0 x 25.0 x 32.5 mm
front_touch_sensor_bracket
front_sensor_button x 2
front_sensor_plate

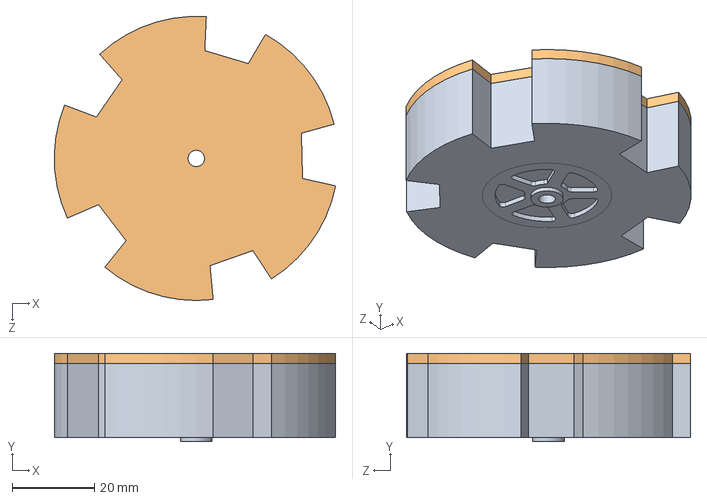
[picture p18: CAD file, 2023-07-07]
CAD/main/neoprene_wheel_cutting_asm.SLDASM
68.3 x 21.4 x 69.0 mm
neoprene_wheel
neoprene_wheel_cutting_tool

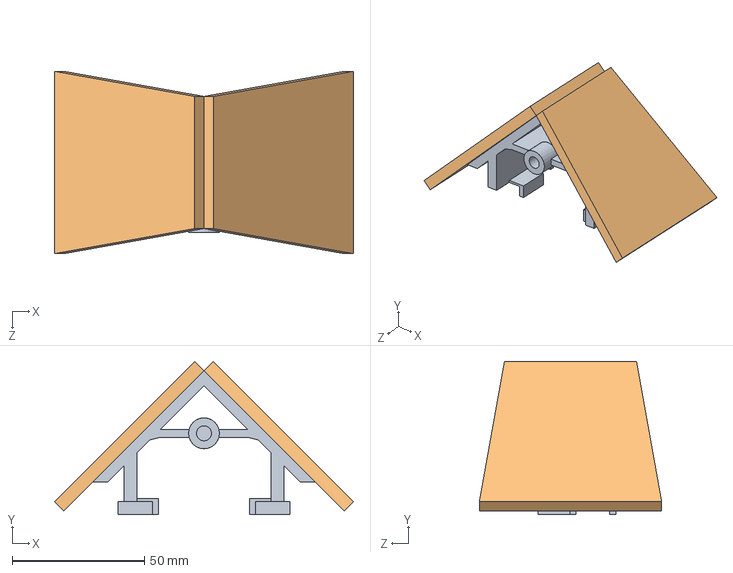
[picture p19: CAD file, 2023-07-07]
CAD/main/mirror_subasm.SLDASM
113.1 x 57.9 x 69.0 mm
mirror_mount
mirror x 2

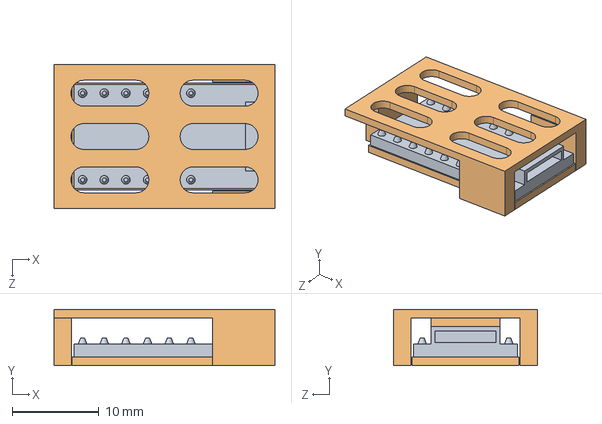
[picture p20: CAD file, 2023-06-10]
CAD/main/encoder_motor_driver_asm.SLDASM
25.5 x 6.50 x 16.6 mm
encoder_motor_driver
Part2^encoder_motor_driver_asm

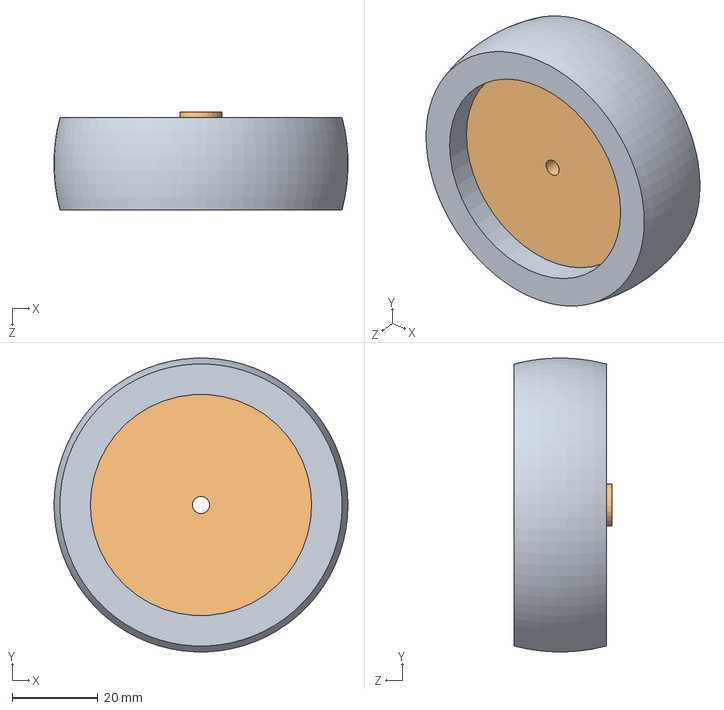
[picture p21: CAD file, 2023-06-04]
CAD/main/makeblock_fat_wheel_asm.SLDASM
68.4 x 68.4 x 22.8 mm
makeblock_fat_tire
wheels

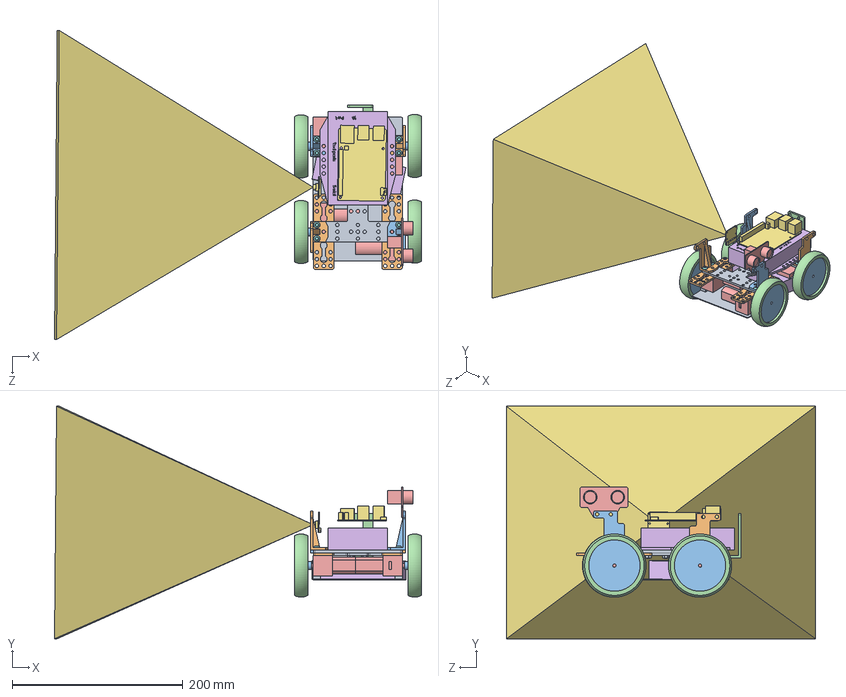
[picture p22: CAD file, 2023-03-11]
CAD/main/robot_asm.SLDASM
429.5 x 272.2 x 362.0 mm
T-bracket x 2
bracket x 2
wheels x 4
tire x 4
encoder_motor x 4
bigscrew x 12
nut x 4
ultrasonic_bracket_left x 2
ultrasonic_bracket_right x 2
ultrasonic_bracket_front
battery
coloursensor
undercover

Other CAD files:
CAD/main/maze.SLDASM
CAD/main/robot_asm_standing.SLDASM
CAD/main/robot_asm_idea.SLDASM
CAD/main/_FINAL_STL/camera_calibration_switch_mount.STL
CAD/main/Colour_sensor_holders/angle10.STL
CAD/main/Colour_sensor_holders/angle2.5.STL
CAD/main/Colour_sensor_holders/angle5.STL
CAD/main/Colour_sensor_holders/angle7.5.STL
CAD/main/M2.5_screw.SLDPRT
CAD/main/M2_insert.SLDPRT
CAD/main/PRINT/Behållare23.55.STL
CAD/main/PRINT/baseplate_front_insert.STL
CAD/main/PRINT/rack spur rectangular_iso_40mm23.55.STL
CAD/main/PRINT/ultrasonic_bracket_newfront_v2.STL
CAD/main/PRINT/voltage_converter_cover.STL
CAD/main/PRINT/voltage_converter_mount.STL
CAD/main/T-bracket.SLDPRT
CAD/main/_FINAL_STL/_Behållare_31-05-23.STL
CAD/main/_FINAL_STL/_R_batteryholder.STL
CAD/main/_FINAL_STL/_R_colour_sensor_holder_10deg.STL
CAD/main/_FINAL_STL/_R_ultrasonic_bracket_newfront.STL
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

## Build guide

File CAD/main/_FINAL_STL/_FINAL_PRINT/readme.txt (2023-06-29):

Do not use these files unless you know what you are doing.
They are sliced for a prusa mini (+), and even if you have the same model of printer, the settings you want to use may differ.
If you want to print the robot, slice the .STL-files yourself.

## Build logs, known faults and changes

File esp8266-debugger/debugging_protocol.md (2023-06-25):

# Debugging the low-level robot code
This collection of programs will enable wireless debugging of low-level robot code.
An ESP8266 (ESP-01 module) will listen for serial data coming from the auriga. This data will then be relayed via websockets to a python program, which reads the data and formats it according to the standard defined in this document. It writes these forwarded messages to a log file, to enable easy debugging.

# Communication between auriga and ESP8266
## The data to send
- Everything being sent to the raspberry pi
- Loop times
- Sensors and pose:
    - Ultrasonic sensor distances
        - Raw
        - Smoothed
    - Robot pose
    - Floor colour
    - Wall presence variables
        - Raw individual
        - Smoothed individual
        - Actual (combined)
    - Distances driven:
        - Dumb distance driven
        - True distance driven
- Detected wallchanges
    - Raw
    - Smoothed
- Stoppingreason
- Blue tile delay
- Recognised checkpoint
- Rescue kit deployment

## How to format it
All commands will begin with \# and end with \\n.

- Pi commands: #pi,\<data>
- Sensors and pose: #s
    - Ultrasonic distances: #s,u\<type>,\<dataF>,\<dataLF>,...,\<dataRB> (F,LF,LB,RF,RB)
        - Raw: type = r
        - Smoothed: type = s
    - Robot pose - #s,p,\<angle>,\<walldistance>
    - Floor colour - "s,f,\<colour>
        - v - white
        - s - black
        - b - blue
        - r - reflective
        - u - unknown
        - n - not updated (maybe not needed)
    - Wall presence: #s,w\<type>,\<data>
        - Raw: type = r. Same data order as raw ultrasonic sensors
        - Smoothed: type = s. Same data order as Raw.
        - Actual (both sensors): type = a. Data order F,L,R
- Wallchanges: #w\<type>,\<data> - data is delivered in the same order as ultrasonic distances
    - Raw - type = r
    - Smoothed - type = s

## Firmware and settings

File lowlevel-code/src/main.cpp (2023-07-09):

// This is the main program for the Auriga


#include <robot_lowlevel.h>
#include <colour_sensor.h>
#include <Arduino.h>
//#include <MeAuriga.h> //DO NOT INCLUDE!!! This was causing the problem all along! The only include of the MeAuriga.h is in robot_lowlevel.cpp. Investigate.
#include <Wire.h>
#include <SPI.h>

#define PICODE
// #define TESTING_NAV
// #define TESTING
// #define COLSENS_CALIBRATION

#ifdef COLSENS_CALIBRATION
#define TESTING
#endif

extern ColourSensor colSensor; // The colSensor object in robot_lowlevel.cpp
extern RobotPose pose;
extern double BASE_TURNING_SPEED;
extern double g_pidSetPoint;

HardwareButton colCalButton {30, false};

void setup()
{
  // Init serial for debugging
  #ifdef PICODE
  Serial.begin(9600);
  #else
  Serial.begin(9600);
  #endif
  
  // Init hardware
  lightsAndBuzzerInit();
  lights::activated();

  gyroInit();
  encodersInit();
  initColourSensor();
  servoSetup();
  flushDistanceArrays();
  fillRampArrayFalse();
  // startDistanceMeasure(); // Why is this here?

  // #warning Debugging
  // checkSmoothWallChanges();
  // checkPotWallChanges();
  

  // Wait for beginning (to give time to remove hands etc.)
  if (colCalButton.isPressed())
  {
    colSensor.clearCalibrationData();
    serialcomm::sendColourCal(); // So that Markus can start the scoring run timer
    while(colCalButton.isPressed())
    {
      colSensor.calibrationRoutineLoop();
    }
    delay(20);
    lights::turnOff();
  }
  delay(100);
  sounds::startupSound();
  serialcomm::sendLOP();
}

// Why are these here?
// double robotAngle = 0;
// double wallDistance = 0;




void loop()
{

  static bool shouldDelay = false;
  resetWallChanges();
  
  #ifdef TESTING
 
  // Command command = serialcomm::readCommand();
  // if (command != command_invalid)
  // {
  //   delay(1000);
  //   serialcomm::returnSuccess();
  // }
  // else sounds::errorBeep();

  // delay(20);
  // serialcomm::clearBuffer();

  // deployRescueKit();
  // delay(2000);

  // getUltrasonics();
  // checkWallPresence();
  
  // driveStep();
  // Serial.println("");Serial.println("------------------------------------------------------------------------------");Serial.println("");
  
  // delay(1500);
  // lights::turnOff();
  // delay(500);

  // IMPORTANT!!! ----------------------------------------------------------------------------------------------------------------------------------------------------------------
  // I tried to change the usmt

  // lights::indicateBlueCircle();
  // lights::turnOff();
  // pose.update();
  // if (abs(pose.xDist - 15) > 3)
  // {
  // sideWiggleCorrection();
  // }
  // delay(2000);
  // lights::turnOff();

  // int multiplier = 1;
  // bool stopMoving = true;
  // double turnStepAngle = 10;
  // awareGyroTurn(-multiplier*turnStepAngle/2.0, stopMoving, 20, false, 0);
  // awareGyroTurn(-multiplier*turnStepAngle/2.0, stopMoving, 11, false, 15);
  // awareGyroTurn(multiplier*turnStepAngle*1.5, stopMoving, 20, false, 0);
  // awareGyroTurn(multiplier*turnStepAngle/2.0, stopMoving, 11, false, -15);
  // awareGyroTurn(-multiplier*turnStepAngle, true, 30, false, 0);
  // delay(1000);

  // getUltrasonics();
  // printUltrasonics();
  // startDistanceMeasure();
  // while(true)
  // {
  //   delay(20);
  //   loopEncoders();
  //   Serial.println(getDistanceDriven());
  // }
  driveStep();
  delay(2000);
  

  #else
  #ifdef PICODE
  if (shouldDelay==true)
  {
  delay(200);
  }
  lights::turnOff();
  #endif
  #ifdef TESTING_NAV
  // For testing without the Pi:
  Command command = command_none;
  flushDistanceArrays();
  makeNavDecision(command);
  // printUltrasonics();
  command = command_driveStep; // For debugging
  delay(555);
  lights::turnOff();
  #endif
  

  // Add some kind of error correction or checking?
  // Potential problem: Some bytes sent over serial may have some additional meaning, thus rendering them inappropriate for use by us
  // Use an enum instead of integers? The enum will be easier to decipher and the integer representation could still be the same
  #ifdef PICODE
  if (Serial.available() != 0)
  {
    Command command = serialcomm::readCommand(false);
    lights::turnOff();
    // sounds::errorBeep();
    #endif
    switch (command)
    {
      // case command_none:
      //   // sounds::tone(440, 50);
      //   lights::noComm();
      //   break;
      // Driving
      case command_driveStep: // drive one step forward
      {
        serialcomm::returnSuccess(); // For validation and robustness of the communication protocol
        g_pidSetPoint = 15;
        // lights::showDirection(lights::front);
        bool continuing = false;
        bool rampDriven = false;
        FloorColour floorColourAhead = floor_notUpdated;
        double xDistanceOnRamp = 0;
        double yDistanceOnRamp = 0;
        driveStepBegin: // Label to be able to use goto statements
          TouchSensorSide frontSensorDetectionType = touch_none;
          bool commandSuccess = driveStep(floorColourAhead, rampDriven, frontSensorDetectionType, xDistanceOnRamp, yDistanceOnRamp, continuing);
          // bool commandSuccess = true;
          // lights::turnOff();
          if (floorColourAhead == floor_black || frontSensorDetectionType == touch_both)
          {
            lights::reversing();
            driveStep(); // For driving back
            // commandSuccess = true; // Not really, but Markus program wants it
          }

          if (frontSensorDetectionType == touch_left)
          {
            // Correct by turning right
            awareGyroTurn(-18, true, BASE_TURNING_SPEED, true, -5);
            awareGyroTurn(-8, true, BASE_TURNING_SPEED, true, 5);
            continuing = true;
            g_pidSetPoint = 20;
            goto driveStepBegin;
            
          }
          else if (frontSensorDetectionType == touch_right)
          {
            // Correct by turning left
            awareGyroTurn(18, true, BASE_TURNING_SPEED, true, -5);
            awareGyroTurn(8, true, BASE_TURNING_SPEED, true, 5);
            continuing = true;
            g_pidSetPoint = 10;
            goto driveStepBegin;
          }

          if (floorColourAhead == floor_blue)
          {
            lights::indicateBlueCircle();
          }
          else if (floorColourAhead == floor_reflective)
          {
            lights::indicateCheckpoint();
            
          }
          // Serial.print("Floor colour ahead: ");
          // Serial.println(floorColourAhead);
          // If we have moved, mazenav has to know the new colour. If we have not moved, the colour is already known.
          if (commandSuccess == true || (floorColourAhead == floor_black)) //  || floorColourAhead == floor_black || floorColourAhead == floor_blue // Removed because it would return success every time it saw blue or black, regardless if it had driven a step or not.
          {
            if (floorColourAhead == floor_black) rampDriven = false;
            Serial.print("!a,");
            Serial.print(colSensor.floorColourAsChar(floorColourAhead)); // If you have not driven back floorColourAhead will actually be the current tile
            Serial.print(',');
            if (rampDriven == true)
            {
              Serial.print("1,");
              Serial.print(xDistanceOnRamp, 0);
              Serial.print(',');
              Serial.print(yDistanceOnRamp, 0);
            } 
            else Serial.print("0");
            Serial.println("");
            // serialcomm::returnFloorColour(floorColourAhead); // Interpreted as success by mazenav (except for black tile)
          }
          else
          {
            serialcomm::returnFailure();
          }
          // if (pose.yDist > 15) pose.yDist -= 30; // Just set to 0 instead?
          pose.yDist = 0; // To prevent the robot driving too far? This could help
          shouldDelay = true;
          g_pidSetPoint = 15;
      }
        break;

      case command_driveBack: // drive one step backwards. Only used for testing/debugging
        shouldDelay = false;
        driveBlind(-30, false);
        stopWheels();
        serialcomm::returnSuccess();
        break;

      case command_turnLeft: // turn counterclockwise one step
        shouldDelay = false;
        serialcomm::returnSuccess();
        // lights::showDirection(lights::left);
        turnSteps(ccw, 1, BASE_TURNING_SPEED);
        
        // sounds::tone(440, 100);
        // lights::turnOff();
        serialcomm::returnSuccess();
        break;

      case command_turnRight: // turn clockwise one step
        shouldDelay = false;
        serialcomm::returnSuccess();
        // lights::showDirection(lights::right);
        turnSteps(cw, 1, BASE_TURNING_SPEED);
        // sounds::tone(880, 100);
        // lights::turnOff();
        serialcomm::returnSuccess();
        break;
      
      // Sensors
      case command_getWallStates: // Send the current state of the walls to the maze code (raspberry). The form is 0bXYZ, where X, Y, Z are 0 or 1, 1 meaning the wall is present. X front, Y left, Z right.
        {
          shouldDelay = false;
          uint8_t wallStates = getWallStates();
          serialcomm::returnAnswer(wallStates);
          break;
        }

      case command_dropKit:
        shouldDelay = false;
        serialcomm::returnSuccess();
        handleVictim(false);
        serialcomm::returnSuccess();
        break;

      case command_light:
        shouldDelay = false;
        // Execute the lighting (including delay)
        serialcomm::returnSuccess();
        lights::execLightCommand();
        lights::turnOff();
        serialcomm::returnSuccess();
        break;

      case command_invalid:
        shouldDelay = false;
        sounds::errorBeep();
        serialcomm::returnFailure();
        break;

      default:
        // Do nothing
        break;
      
    }
    serialcomm::clearBuffer();
  #ifdef PICODE
  }
  #endif

  #endif


}

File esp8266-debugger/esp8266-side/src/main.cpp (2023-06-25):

#include <Arduino.h>
#include <ESP8266WiFi.h>
#include <ESP8266mDNS.h>
#include <WebSocketsServer.h>
// #include <ESP8266WiFiMulti.h>

// ESP8266WiFiMulti wifiMulti;
WebSocketsServer webSocket(81); // Define the socket

// For the AP that will be created
const char *ssid = "ESP8266 debugger";
const char *password = "edrobotics";

IPAddress local_IP(192, 168, 1, 5);
IPAddress gateway(192, 168, 1, 1);
IPAddress subnet(255, 255, 255, 0);

const char* mdnsName = "esp-debugger";


void yeildingDelay(long delayTime)
{
  for (int i=0; i<delayTime/50; ++i)
  {
    yield();
    delay(50);
  }
}

void startWiFi()
{
  WiFi.softAPConfig(local_IP, gateway, subnet);
  WiFi.softAP(ssid, password);

  while (WiFi.softAPgetStationNum() < 1) {delay(100);}

}

void webSocketEvent(uint8_t num, WStype_t type, uint8_t * payload, size_t length)
{
  switch (type)
  {
    case WStype_DISCONNECTED:
      break;
    
    case WStype_CONNECTED:
      webSocket.sendTXT(num, "[INFO] Server-client connection established");
      // webSocket.broadcastTXT("Server connected to client");
      break;
    
    case WStype_TEXT:
      // Do nothing, as the server is only sending
      break;

    case WStype_BIN:
      // Do nothing, as the server is only sending
      break;
  }
}

void startWebSocket()
{
  webSocket.begin();
  webSocket.onEvent(webSocketEvent);
}


void startMDNS()
{
  if (!MDNS.begin(mdnsName))
  {
    // Serial.println("Error setting up MDNS responder");
  }
  // else Serial.println("Started mdns responder");
}


void sendSocketData(String data)
{

}

void setup() {
  Serial.begin(115200);
  Serial.println("");

  startWiFi();
  // Serial.println("WiFi began...");

  startWebSocket();
  // Serial.println("Started websocket");

  startMDNS();
  // Serial.println(WiFi.softAPIP());

}

void loop() {
  webSocket.loop();
  MDNS.update();
  if (Serial.available() > 0)
  {
    String readString;
    readString = Serial.readStringUntil('\n');
    webSocket.broadcastTXT(readString);
  }
  
}

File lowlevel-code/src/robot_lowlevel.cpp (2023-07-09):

// Provides most functions for main.cpp

#include <robot_lowlevel.h>
#include <colour_sensor.h>
// #include <ultrasonic_sensor.h>
#include <Arduino.h>
#include <MeAuriga.h>
#include <Servo.h>
#include <FastLED.h> // For the camera light
// #include <MeEncoderOnBoard.h>
#include <MeGyro.h>
#include <Wire.h>
#include <SPI.h>

// Encoder motor definitions
// Make an array of them? Could I then call encoderArray.loop() to loop all sensors?
MeEncoderOnBoard encoderLF(SLOT2); // Left front encoder motor
MeEncoderOnBoard encoderLB(SLOT3); // Left back encoder motor
MeEncoderOnBoard encoderRF(SLOT1); // Right front encoder motor
MeEncoderOnBoard encoderRB(SLOT4); // Right back encoder motor

// Servo
Servo servo;

// Ultrasonic sensor definitions
MeUltrasonicSensor ultrasonicF(PORT_6);   // Front
MeUltrasonicSensor ultrasonicLF(PORT_8);  // Left front
MeUltrasonicSensor ultrasonicLB(PORT_9);  // Left back
MeUltrasonicSensor ultrasonicRF(PORT_7);  // Right front
MeUltrasonicSensor ultrasonicRB(PORT_10); // Right back
MeUltrasonicSensor ultrasonicSensors[] =
    {
        ultrasonicF,
        ultrasonicLF,
        ultrasonicLB,
        ultrasonicRF,
        ultrasonicRB};

RGBColour colourBlack{0, 0, 0};
RGBColour colourWhite{100, 100, 100};
RGBColour colourBase{5, 42, 0};
RGBColour colourOrange{42, 5, 0};
RGBColour colourRed{150, 0, 0};
RGBColour colourBlue{0, 0, 150};
RGBColour colourError{200, 10, 0};
RGBColour colourAffirmative{20, 150, 0};
RGBColour colourYellow{50, 50, 0};
RGBColour colourPurple{100, 0, 150};

// Colour sensor:
ColourSensor colSensor;

// Gyro definition
MeGyro gyro(0, 0x69);

// Buzzer (for debugging)
MeBuzzer buzzer;

// RGB ring
MeRGBLed ledRing(0, 12);

const double MAX_CORRECTION_DISTANCE = 16;
const double MIN_CORRECTION_ANGLE = 8;
const double MAX_WALLCHANGE_ANGLE = 25; // Should be changed later to compute the actual distances
const double MAX_WALLCHANGE_DISTANCE;

#warning untuned constants
// const double MAX_ULTRASONIC_FAR = 70; // Max distance to use differences in front ultrasonic sensor distance
const double MAX_ULTRASONIC_NEAR = 21; // Max distance to use absolute value of front ultrasonic sensor
// const double MAX_FRONT_DIFFERENCE = 3; // The maximum allowed difference between two front ultrasonic readings
const double MAX_FRONT_CORRECTION_DISTANCE = 11; // The maximum allowed difference between pose and corrected pose when the front ultrasonic sensor gets involved.
// const double MAX_FRONT_ANGLE = 7; // The maximum allowed angle for the front sensor to be used. Tuned theoretically for 120cm far distance
#warning If stopping too early, either ignore or drive back saying it is blocked (could be an obstacle)

/*
enum TurningDirection {
    cw,
    ccw,
};
enum WheelSide {
    wheels_left,
    wheels_right,
};
*/

//---------------------- Variable definitions ----------------------------//

// Wheel and wheelbase dimensions (all in cm)
const double WHEEL_DIAMETER = 6.8;
const double WHEEL_CIRCUMFERENCE = PI * WHEEL_DIAMETER;

// Driving
const double CMPS_TO_RPM = 1.0 / WHEEL_CIRCUMFERENCE * 60.0;  // Constant to convert from cm/s to rpm
const double BASE_SPEED_CMPS = 18;                            // The base speed of driving (cm/s)
const double TURBO_SPEED_CMPS = 21;
double BASE_TURNING_SPEED = 46 / CMPS_TO_RPM;                 // The turning speed to normally use
double g_baseSpeed_CMPS = BASE_SPEED_CMPS;                    // The speed to drive at
const double BASE_SPEED_RPM = CMPS_TO_RPM * g_baseSpeed_CMPS; // The base speed of driving (rpm)
double g_trueDistanceDriven = 0;                              // The correct driven distance. Measured as travelling along the wall and also updated when landmarks are seen
double g_targetDistance = 0;                                  // The distance that you want to drive
double g_startDistance = 0;                                   // The distance that you start from

// For potential wallchanges.
// First dimension: which sensor to use. ultrasonic_F (0) is unused
// Second dimension: wallchange_approaching or wallchange_leaving
// Should initialize all structs empty
PotWallChange g_potWallChanges[ULTRASONIC_NUM][2]{};
WallChangeType g_smoothWallChanges[ULTRASONIC_NUM]{};

// The offset from what should be correct when correcting with wallchanges

// Sensor constants
const double ULTRASONIC_FORWARDOFFSET = 7.3;
const double ULTRASONIC_SPACING = ULTRASONIC_FORWARDOFFSET * 2; // The distance between the centers two ultrasonic sensors on the same side.
#warning uncalibrated constants
const double ULTRASONIC_SIDEOFFSET = 7;
const double ULTRASONIC_FRONT_OFFSET = 9.5;     // The distance from the front sensor to the center of the robot
const double ULTRASONIC_DISTANCE_TO_WALL = 7.1; // The distance between the ultrasonic sensor (edge of the robot) and the wall when the robot is centered.
const double WALL_PRESENCE_TRESHOLD = 20;       // Not calibrated !!!!!!!!!!!!!!!!!!!!!!!! Just a guess!!!!!!!!!!!!!!!!!!!!!!!
const double FRONT_WALL_STOPPING_TRESHOLD = 15 - ULTRASONIC_FRONT_OFFSET + 1.8;

// Wallchange offsets for original wheels
// double wallChangeOffsets[wcoff_num] =
// {
//   3.5,  // frontLeaving
//   -0.5, // frontApproaching
//   3,    // backLeaving
//   0     // backApproaching
// };

// Wallchange offsets for neoprene foam wheels
double wallChangeOffsets[wcoff_num] =
    {
        2,    // frontLeaving
        -1.5, // frontApproaching
        5.3,    // backLeaving
        -0.5  // backApproaching
};
double wallChangeOffsetsSmooth[wcoff_num] =
    {
        4.3,  // frontLeaving
        -0.1, // frontApproaching
        4.4,    // backLeaving
        -1.5  // backApproaching
};

const double BACK_WALLCHANGE_DISTANCE = 15 + ULTRASONIC_SPACING / 2.0;
const double FRONT_WALLCHANGE_DISTANCE = 15 - ULTRASONIC_SPACING / 2.0;

// Array containing the order in which the sensors should be called
UltrasonicSensorEnum ultrasonicCallingOrder[ULTRASONIC_NUM] =
    {
        ultrasonic_LF,
        ultrasonic_RB,
        ultrasonic_RF,
        ultrasonic_LB,
        ultrasonic_F,
};

// Array containing the raw distances of the sensors. It keeps the latest values (how many is determined by (DISTANCE_MEASUREMENT_SIZE))
// First dimension: Which ultrasonic sensor to use
// Second dimension: Which value to access
double ultrasonicRawDistances[ULTRASONIC_NUM][DISTANCE_MEASUREMENT_SIZE]{}; // Initializes all distances to 0
// This array contains the pointers for keeping track of which value in the raw distance array is the latest.
int ultrasonicRawDistancesPointer[ULTRASONIC_NUM]{};

// Contains the most recent raw and smooth distances
// First dimension: Which sensor to use
// Second dimension: Which data type to use (usmt_raw or usmt_smooth)
double ultrasonicCurrentDistances[ULTRASONIC_NUM][USMT_NUM]{};
// double ultrasonicLastKnownDistances[ULTRASONIC_NUM][USMT_NUM] {};
double ultrasonicTheoreticalDistances[ULTRASONIC_NUM]{};
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

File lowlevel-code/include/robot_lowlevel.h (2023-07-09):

// Header file

#ifndef ROBOT_LOWLEVEL_H
#define ROBOT_LOWLEVEL_H

// #include <Arduino.h>
// #include <MeAuriga.h>
// #include <MeEncoderOnBoard.h>
// #include <MeGyro.h>
#include <colour_sensor.h>

const int ON_RAMP_ARR_SIZE = 5;

enum UltrasonicSensorEnum
{
  ultrasonic_F,
  ultrasonic_LF,
  ultrasonic_LB,
  ultrasonic_RF,
  ultrasonic_RB,
  ULTRASONIC_NUM, // The number of ultrasonic sensors
};

enum US_MeasurementType
{
  usmt_raw,
  usmt_smooth,
  USMT_NUM,
};


enum WallChangeOffsets
{
  wcoff_frontLeaving,
  wcoff_frontApproaching,
  wcoff_backLeaving,
  wcoff_backApproaching,
  wcoff_num,
};

enum TouchSensorSide
{
  touch_none,
  touch_left,
  touch_right,
  touch_both
};


//////////////// Public functions /////////////////////////////

// Drives one step (30cm) forwards.
// Could take a speed argument
// continuing - if you should continue where you left off last time (keeping the truedistancedriven)
bool driveStep(FloorColour& floorColourAhead, bool& rampDriven, TouchSensorSide& frontSensorDetectionType, double& xDistanceOnRamp, double& yDistanceOnRamp, bool continuing);

bool driveStep();

enum TurningDirection {
    cw,
    ccw,
};

// Turns the specified amount of steps.
// steps - the amount of steps (90 degrees) to turn. Positive is counter-clockwise, negative is clockwise.
// The direction may be separated into a separate argument and given its own type.
void turnSteps(TurningDirection direction, int steps, double turningSpeed);

// Returns an byte giving information about whether the walls are present
int getWallStates();


enum Command
{
  command_driveStep,
  command_driveBack, // Should not be used.
  command_turnLeft,
  command_turnRight,
  command_getWallStates,
  command_interrupt,
  command_resume,
  command_dropKit,
  command_light,
  command_invalid,
  command_none,
};

namespace serialcomm
{
    void returnSuccess();

    void returnFailure();

    void returnFloorColour(FloorColour floorColour);

    void returnAnswer(int answer);

    // char readChar();
    // Read a command following the outlined standard
    // Returns data of type Command.
    // Command readCommand();

    Command readCommand(bool waitForSerial);
    Command readCommand (bool waitForSerial, int timeout);

    void clearBuffer();

    bool checkInterrupt();
    bool checkDebugInterrupt();

    void answerInterrupt(int stepDriven);

    void cancelInterrupt();

    // Sends data that will be printed to the console / other debugging method
    // Should accept types in the same way that Serial.print() does.
    bool sendDebug();

    void sendLOP();

    void sendColourCal();
}

class BumperComm
{ 
  public:
    void communicate();
    void setInitiator(bool isInit);
    int readKitNum[4] {0};
    int writeKitNum[4] {0};
  private:
    bool isReady(); // Determines if the other robot is present and thus if communication can be initiated
    void receiveData(); // Receive data once ready
    void transmitData(int kits); // Transmit data once ready
    void endCommunication(); // Returns the robot to its original state (middle of the tile)

    void gotoReadPos();
    int read();
    void gotoWritePos();
    void write(int kits);
    void returnToNeutral(); // Return to the middle of the tile

    bool bumpDriveLoop(bool backwards); // False is forwards, true is backwards. Loop it.

    bool isActivated();
    long timeFlag = 0;

    const int BASE_LEN = 1000; // The length of a rescue kit sending
    const int CONTACT_LEN = 1000; // The length of contact for one sending
    const int SHORT_PAUSE_LEN = 1000; // The length of the pause between bumps in a kit
    const int LONG_PAUSE_LEN = 3000; // The length of the pause between kits
    const int MIN_DEBOUNCE_TIME = 700; // The time for which to block bumpreadings
    
    bool isInitiator = false; // True if this robot should initiate, false if it should not (the other robot initiates)
    double ROBOT_DETECTION_THRESHOLD = 20;
    bool inReadPos = false;
    bool inWritePos = false;
    double beginUltrasonicDist;
    bool blockFrontSensor = false;
};

// Makes a navigation decision
// For simple testing without the maze-code present
void makeNavDecision(Command& action);



void lightsAndBuzzerInit();

struct RGBColour
{
    int red;
    int green;
    int blue;
};

namespace lights
{
    enum LedDirection
    {
        front = 0,
        left = 3,
        right = 1,
        back = 2,
    };

    enum LightCommand
    {
      lCommand_done,
      lCommand_returning,
      lCommand_notReturning,
      lCommand_mappingError,
      lCommand_navigationFail,
      lCommand_none
    };

    LightCommand getLightCommandFromChar(char command);
    void execLightCommand();

    // Turns all lights off
    void turnOff();
    void showCustom();

    void setColour(int index, RGBColour colour, bool showColour);
    void setColour(int index, RGBColour colour, double intensity, bool showColour);
    RGBColour safeMltp(RGBColour base, double multiplier);

    // Shows the 3 leds facing in the requested direction
    void showDirection(LedDirection direction);
    void showDirection(lights::LedDirection direction, RGBColour colour);

    void fastBlink(RGBColour colour);

    void affirmativeBlink();

    void errorBlink();

    void noComm();

    void negativeBlink();
    
    void floorIndicator(FloorColour floorColour);
    
    void disabled();

    void activated();

    void checkPointRestored();

    void turnOnVictimLights(bool show);

    void indicateFrontSensor();

    void reversing();

    void onRamp();

    void indicateCheckpoint();

    void rampDriven();

    int safeIndex(int index);
    
    // Produces a spinning circle animation
    // colour is RGBColour
    // speed - the speed at which the ring travels in rounds per second
    void circleLoop(RGBColour colour1, RGBColour colour2, double speed);
    void circle(RGBColour colour1, RGBColour colour2, double speed, int duration);
    void indicateBlueCircle();

}

namespace sounds
{
    // Silence all sound
    void silence();

    // Beep indicating an error. Should maybe accept an error type as an argument?
    void errorBeep();

    void tone(int freq, int duration);

    void startupSound();
}

void initColourSensor();


/////////////////// Private functions /////////////////////////////





//---------------- Low level encoder motor functions ---------------------//


// Encoder interrupt processes:
void isr_encoderLF(void);
void isr_encoderLB(void);
void isr_encoderRF(void);
void isr_encoderRB(void);


// Loop all encoders
void loopEncoders();

// Most of (all?) the code needed to initialize the encoders
// Should be run inside of setup()
void encodersInit();

//--------------------- Slightly higher level encoder motor functions --------------------------//

// Stop the specified wheel
// wheel - the wheels to stop. An integer for now, but could be a user defined type later. Take an object as argument?
void stopWheels();
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

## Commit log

2023-03-02 transferred already existing CAD files
    [T-bracket.SLDPRT, auriga_board.SLDPRT, baseplate.SLDPRT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]
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2023-03-06 transferred old code and removed file separation because of bugs
    [main.cpp]
2023-03-07 added battery holder to undercover_new
    [auriga_board.SLDPRT, baseplate.SLDPRT, battery.SLDPRT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]
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2023-03-09 switched interface to maze code to use integers and added independent testing
2023-03-11 updated equation file references and wheel dimensions
    [T-bracket.SLDPRT, auriga_board.SLDPRT, baseplate.SLDPRT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]
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2023-03-15 did various CAD updates
    [auriga_board.SLDPRT, battery.SLDPRT, bigscrew.SLDPRT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]
2023-03-19 redesign begun
    [auriga_board.SLDPRT, back_handle_ultrasonic-mount.SLDPRT, baseplate.SLDPRT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]
2023-03-22 finished basic redesign
    [auriga_board.SLDPRT, baseplate.SLDPRT, baseplate_v1.STL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]
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2023-03-23 fixed angle drifting bug
    [robot_lowlevel.cpp]
2023-03-23 Socket server reads strings correctly, general improvements
2023-03-26 added front touch sensor + misc fixes
    [auriga_board.SLDPRT, baseplate.SLDPRT, batteryholder.SLDPRT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]
2023-03-27 added voltage converter + misc
    [auriga_board.SLDPRT, baseplate.SLDPRT, batteryholder.SLDPRT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]
2023-03-28 added misc updates
    [auriga_board.SLDPRT, baseplate.SLDPRT, batteryholder.SLDPRT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]
2023-03-28 updated mirror mount
    [auriga_board.SLDPRT, baseplate.SLDPRT, batteryholder.SLDPRT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]
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2023-03-29 added rescue kit mechanism
    [BaseplateRescuekit23.35.SLDPRT, BaseplateRescuekit23.55.SLDPRT, Behållare23.55.SLDPRT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]
2023-03-30 finished rescue kit mechanism
    [auriga_board.SLDPRT, baseplate.SLDPRT, baseplate_v2.3mf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]
2023-03-30 finalized design
    [Behållare23.55.STL, auriga_board.SLDPRT, baseplate.SLDPRT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]
2023-03-30 improved victim signalling when not dropping kits
    [auriga_board.SLDPRT, auriga_spacer.SLDPRT, auriga_spacer.STL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]
2023-03-31 added driving backwards, introductions to it and more
    [baseplate.SLDPRT, baseplate_front_insert.SLDPRT, baseplate_v3.STL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]
2023-03-31 collection of the latest code commits (wrongfully done as CAD)
    [colour_sensor.cpp, colour_sensor.h, main.cpp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]
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2023-05-09 fixed new wallchange system
    [main.cpp, robot_lowlevel.cpp, robot_lowlevel.h]
2023-05-09 added straightening (angle correction)
    [colour_sensor.cpp, robot_lowlevel.cpp, robot_lowlevel.h]
2023-05-25 added x and y distance on rammps and began frontSensor avoidance
    [colour_sensor.cpp, main.cpp, robot_lowlevel.cpp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]
2023-05-25 finished code for partial frontal collision (UNTESTED)
    [main.cpp, robot_lowlevel.cpp, robot_lowlevel.h]
2023-05-28 added ramp x and y distance, advanced collision detection + correction, half-done colour calibration routine
    [colour_sensor.cpp, colour_sensor.h, main.cpp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]
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2023-06-02 finished mirror mount, colour sensor mount and more. Camera light begun + misc.
    [Behållare23.55.SLDPRT, auriga_board.SLDPRT, baseplate.SLDPRT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]
2023-06-02 added rescue-kit mechanism interface to baseplate
    [auriga_board.SLDPRT, baseplate.SLDPRT, baseplate_front_insert.SLDPRT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]
2023-06-02 added mounting for camera light and made fat makeblock wheels
    [auriga_board.SLDPRT, baseplate.SLDPRT, baseplate_front_insert.SLDPRT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]
2023-06-04 finished Pi mounting, moved front ultrasonic forward 1mm + misc.
    [M2_insert.SLDPRT, auriga_board.SLDPRT, baseplate.SLDPRT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]
2023-06-04 finished mirror mounting
    [camera_holder_bar.SLDPRT, front_handle_ultrasonic-mount.SLDPRT, handle_BR.STL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]
2023-06-04 added support for LED ring board
    [camera_holder_bar.SLDPRT, front_handle_ultrasonic-mount.SLDPRT, raspberrypi_4.SLDPRT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]
2023-06-05 added colour to the robot
    [robot_asm_baseplate.SLDASM, ultrasonic_sensor.SLDPRT]
2023-06-05 added battery cable hook
    [auriga_board.SLDPRT, baseplate.SLDPRT, baseplate_front_insert.SLDPRT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]
2023-06-05 added rescue kit mechanism baseplate
    [camera_holder_bar.SLDPRT, camera_holder_bar_v4.STL, colour_sensor_holder_new.SLDPRT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]
2023-06-05 fixed camera ledring cable routing + tolerances
    [camera_LEDring_casing.SLDPRT, camera_LEDring_casing_inner_v2.STL, camera_LEDring_with_casing.SLDASM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]
2023-06-05 state of objects as of printing
    [baseplate.SLDPRT, baseplate_front_insert.SLDPRT, baseplate_v4.STL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]
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2023-06-07 fixed bug with not staying after dropping kits
    [main.cpp, robot_lowlevel.cpp]
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2023-06-07 added component list
    [component_list.xlsx]
2023-06-08 did serial communication fixes
    [main.cpp, robot_lowlevel.cpp, robot_lowlevel.h]
2023-06-08 began working on mounting for the neoprene foam wheels
    [neoprene_mount_asm.SLDASM, neoprene_wheel_mounting.SLDPRT, neoprene_wheel_mounting_test.STL]
2023-06-10 added encoder motor driver + housing (unfinished measurements)
    [auriga_board.SLDPRT, baseplate.SLDPRT, batteryholder.SLDPRT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]
2023-06-12 updated neoprene wheel mounting
    [encoder_motor.SLDPRT, neoprene_wheel_mounting.SLDPRT, neoprene_wheel_mounting.STL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]
2023-06-12 Fixed dropping kits in interrupt
2023-06-12 added two security featuers one to make sure that the victim is on the right heigh and on to look if the victim is moving and keeping shape between different frames (not finished)
2023-06-12 Add files via upload
    12_06_2023 aktuella rescue kit mekanism CAD och STL filer
    [Behållare_08-06-23.STL, Behållare_31-05-23.SLDPRT, Behållare_31-05-23.STL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]
2023-06-13 misc. communication fixes + removed angle correction in wallchanges
    [colour_sensor.cpp, main.cpp, robot_lowlevel.cpp]
2023-06-13 began implementing wiggling corrections
    [robot_lowlevel.cpp, robot_lowlevel.h]
2023-06-14 updated voltage converter mount
    [auriga_board.SLDPRT, baseplate.SLDPRT, batteryholder.SLDPRT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]
2023-06-14 commit because of OneDrive sync error. Communication improvements, reflective tile detection improvements, lighting for dropped rescue kits + began wiggle correction
    [colour_sensor.cpp, main.cpp, robot_lowlevel.cpp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]
2023-06-14 voltage converter updates
    [robot_asm_baseplate.SLDASM, voltage_converter_cover_independent.SLDPRT, voltage_converter_cover_v2.STL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]
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2023-06-14 looked over what happens on a ramp, off one and on both. Also improved serial communication with interrupt cancellation on ramps
2023-06-15 misc. fixes and turbospeed prototype
    [colour_sensor.h, main.cpp, robot_lowlevel.cpp]
2023-06-15 cleanup and error managment
    [visionclass.py]
2023-06-15 added angle correction to wallchanges (untested, may be wrong direction and wrong when reversing)
    [main.cpp, robot_lowlevel.cpp, robot_lowlevel.h]
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2023-06-15 angle correction for wallchanges should work good enough for now
    [main.cpp, robot_lowlevel.cpp]
2023-06-17 added failsafe for turbospeed and tweaked camera light colour
    [main.cpp, robot_lowlevel.cpp]
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2023-06-17 probably implemented new system for robot pose. First compiling version. Untested and probably buggy
    [robot_lowlevel.cpp, robot_lowlevel.h]
2023-06-17 maybe fixed potential bug with gyro offsets
    [robot_lowlevel.cpp]
2023-06-18 added advertising banners and made front sensor wider
    [advertising_banner.SLDPRT, advertising_banner.STL, advertising_banner_front.SLDPRT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]
2023-06-19 CAD updates
    [advertising_banner.SLDPRT, auriga_board.SLDPRT, baseplate.SLDPRT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]
2023-06-19 improved neoprenee foam tire mounting
    [neoprene_wheel_mounting.SLDPRT, neoprene_wheel_mounting_v4.STL]
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2023-06-23 added samples for new SD cards missed it somehow
2023-06-25 weird linux commit
    [neoprene_wheel_mounting.SLDPRT, neoprene_wheel_mounting_v5.STL]
2023-06-25 Updated ramp bit bug, added back to start way finding
    [config.txt]
2023-06-25 Fixed mistake with lower case config
2023-06-25 fixed bug: Wrong pose estimation for right (and dual) wall(s)
    [main.cpp, robot_lowlevel.cpp]
2023-06-26 fixed interrupt bug
2023-06-26 tuned wallchange constants and fixed rampdrive problem
    [robot_lowlevel.cpp]
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2023-06-29 hopefully last CAD work done
    [Behållare_31-05-23.SLDPRT, ServoHållare_03-06-23.SLDPRT, _Behållare_31-05-23.STL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]
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2023-06-29 fixed reflective colour detection
    [main.cpp, robot_lowlevel.cpp]
2023-06-29 added safeguard for dead reckoning when at an angle (missing ramps). Unsure if it fixes (cannot replicate problem)
    [robot_lowlevel.cpp]
2023-06-29 updated ramp correction coefficients
    [robot_lowlevel.cpp]
2023-06-30 Fixed timing??? There should not have been a problem but still
    [config.txt]
2023-06-30 Fixed config
    [config.txt]
2023-06-30 commit due to git error + various updates
    [colour_sensor.cpp, colour_sensor.h, main.cpp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]
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2023-07-01 Made fancier log and config files, fixed ramp mapwayback ramp issue
    [config.cfg]
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2023-07-02 made it easy to switch between split and normal detection of reflective tiles
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2023-07-02 In socket communication, now tries to reset connection when it fails
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2023-07-03 fixed a bug from last commit for real this time (hopefully)
    [visionclass.py]
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2023-07-05 some CAD updates
    [camera_calibration_switch_mount.SLDPRT, camera_calibration_switch_mount.STL, neoprene_wheel_cutting_asm.SLDASM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]
2023-07-05 fixed a problem in logging
    [visionclass.py]
2023-07-05 updated some constants and probably fixed communication bug
    [colour_sensor.cpp, main.cpp, robot_lowlevel.cpp]
2023-07-05 fixed lighting command from raspberry pi
    [robot_lowlevel.cpp]
2023-07-06 removed some debugging and fixed issue when driving backwards
    [colour_sensor.cpp, main.cpp, robot_lowlevel.cpp]
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2023-07-06 fixed wallchange bug and fixed illegal stair problem
    [colour_sensor.cpp, main.cpp, robot_lowlevel.cpp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]
2023-07-07 updated wheel dimensions
    [M2.5_screw.SLDPRT, advertising_banner.SLDPRT, advertising_banner_front.SLDPRT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]
2023-07-07 fixed probable rampDriven detection problem
    [main.cpp, robot_lowlevel.cpp]
2023-07-07 added double turn correction by obstacle
    [main.cpp]
2023-07-08 changed to testing code and added reset of wallchanges
    [main.cpp]
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
